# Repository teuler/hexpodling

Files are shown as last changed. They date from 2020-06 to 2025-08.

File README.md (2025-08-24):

# hexpodling
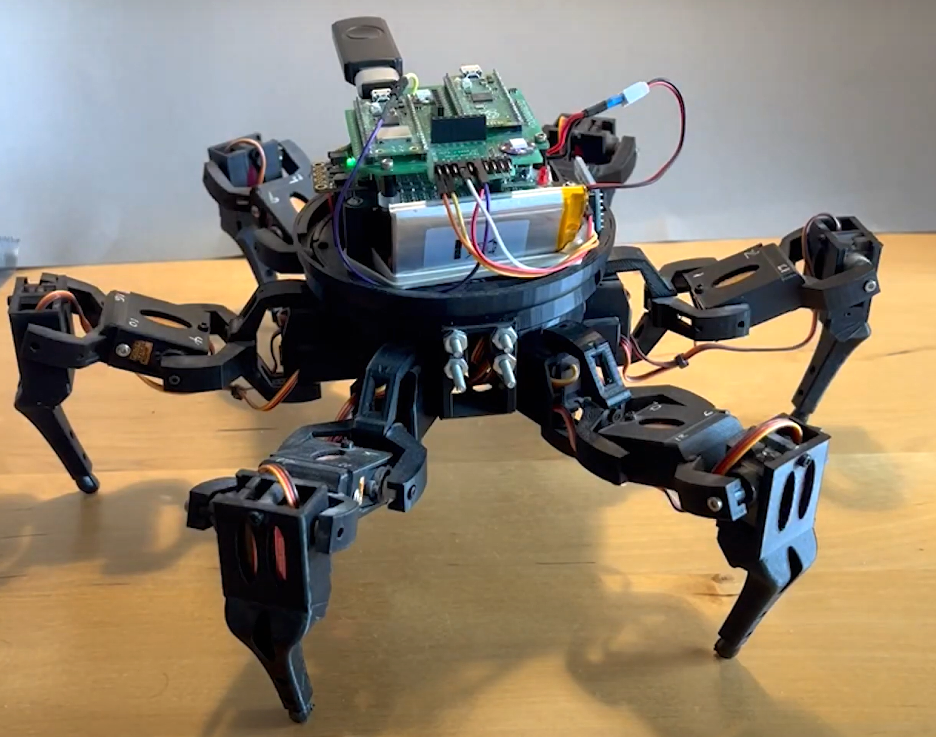
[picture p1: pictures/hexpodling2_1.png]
[](https://github.com/teuler/hexpodling/blob/master/pictures/hexpodling2_1.png)
"hexpodling" is a work-in-progress, 3-degrees of freedom (3DOF) hexapod robot based on the [Vorpal](https://vorpalrobotics.com/wiki/index.php/Vorpal_The_Hexapod) from Vorpal Robotics. The original Vorpal is remote-controlled and 2DOF; it is aimed at teaching in schools. 

The main differences between the original and the version described here are:
* The legs contain an additional segment, hence 3DOF
* Based on [Raspberry Pi Pico microcontrollers](https://www.raspberrypi.com/products/raspberry-pi-pico/) instead of the original's Arduino Nano, with one Pico controlling the movements (server) and one for the "higher" functions (client)
* Programmed in [PicoMite MMBasic](https://geoffg.net/picomite.html) by Peter Mather and Geoff Graham
* Supports current sensing (load) for up to 8 servos, e.g. to detect if the robot is stuck

Here is a [video](https://youtu.be/h_NlpfQ0yDU) demonstrating its movements (remote-controlled).  
For the details, see [Wiki](https://github.com/teuler/hexpodling/wiki).

### Release Notes

* 2025-08-24
  * Sensor head with camera (ESP32-cam) and time-of-flight distance sensor added (see [new wiki page](https://github.com/teuler/hexpodling/wiki/Camera-and-ToF-sensor))
  * new printed parts (sensor head) added
* 2025-01-01 - After a long pause
  * Switched to MMBasic :-)
  * New client board featuring two Pico RP2040 microcontrollers
  * Remote control (to test movements) direcly w/ a wireless XBox controller
* 2020-12-27 - Updates - Still work in progress
  * Wiki pages 'Mechanics' and 'Boards' added
  * Code updated (now also some initial code for the client microcontroller)
  * Both boards - for the "walk engine" and for the "behavior engine" - revised (including bug fixes)
* 2020-06-27 - Initial release

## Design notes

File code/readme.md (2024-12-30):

- `micropython` - the __depreciated__ python code
- `mmbasic`- the current MMBasic code w/ libraries and tools

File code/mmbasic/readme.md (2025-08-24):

This folder contains the current MMBasic code:

- `hps_calibrate.bas` - A tool to calibrate the servo positions of the legs
- `hps_cli.bas` - The main program for the Pico that serves as client (it controls the robot) 
- `hps_srv.bas` - The main program for the Pico that runs the server; it controls the movements of the robot (lets it walk), collects some sensor data about the robots orientation, the voltages of servo and logic batteries, etc.
- `lib_bno055.bas` - "Driver" for the BNO055 9-axis absolute-orientation sensor with sensor fusion.
- `lib_mcp3208.bas` - "Driver" for the MCP3208 chip, an 8-channel 12-bit A/D converter with SPI interface
- `lib_esp32cam.bas` - "Driver" for the ESP32-cam / VL53L5CX time-of-flight sensor
- `lib_keyboard.bas` - Keyboard routines for `hps_cli.bas`
- `lib_maestro.bas` - Routines for servo control via the Pololu 18-channel Maestro board
- `cal_load.dat` - calibration data for the first 4 servo load channels 

## Server
To upload the software to the server Pico:
1. Install the [PicoMite firmware](https://geoffg.net/Downloads/picomite/PicoMite_Firmware.zip) (V6.0x, `PicoMiteRP2350V6.0xxx.uf2`)
2. Load programs onto the internal drive:
   ```
   xmodem r "hps_srv.bas"
   xmodem r "lib_bno055.bas"
   xmodem r "lib_mcp3208.bas"
   xmodem r "lib_maestro.bas"
   xmodem r "hps_calibrate.bas"
   xmodem r "cal_load.dat"
   ```
3. Install libraries:
   ```
   library delete
   load "lib_bno055.bas"
   library save
   load "lib_mcp3208.bas"
   library save
   load "lib_maestro.bas"
   library save
   ```
4. Set the following options:
   ```
   OPTION COLOURCODE ON
   OPTION DISPLAY 64, 80   
   OPTION AUTORUN ON
   OPTION HEARTBEAT OFF
   OPTION CPUSPEED 252000
   ```
5. Now load the main program `hps_srv.bas` and run it.
     
## Client
To upload the software to the client Pico:
1. Install the [PicoMite firmware](https://geoffg.net/Downloads/picomite/PicoMite_Firmware.zip) (V6.0x, `PicoMiteRP2350USBV6.0xxx.uf2t). The USB variant is needed to allow the robot to be controlled by a USB-gamepad.

> Note: _After installing the USB firmware, the Pico console cannot be longer connected via the USB port, because it enters host-mode. For connecting the serial console, use pins GP8 and GP9 (COM2, 115200). For details, see MMBasic manual._

2. Load programs onto the internal drive:
   ```
   xmodem r "hps_cli.bas"
   xmodem r "lib_keyboard.bas"
   xmodem r "lib_esp32cam.bas"
   ```
3. Install libraries:
   ```
   library delete
   load "lib_keyboard.bas"
   library save
   ```
4. Set the following options (note that the SPI and LCDPANEL options are only needed if connecting a TFT display):
   ```
   OPTION SERIAL CONSOLE COM2,GP8,GP9
   OPTION LCD SPI GP18,GP19,GP16
   OPTION COLOURCODE ON
   OPTION HEARTBEAT OFF
   OPTION CPUSPEED 252000
   OPTION DISPLAY 64, 80
   OPTION LCDPANEL ST7789_320BUFF, PORTRAIT,GP22,GP15,GP17,GP14
   OPTION AUTORUN ON
   OPTION PICO OFF
   ```
   Calling `option list` should also give the follwing options automatically:
   ```
   OPTION SERIAL CONSOLE COM2,GP8,GP9
   OPTION KEYBOARD US
   ```
   
5. Now load the main program `hps_cli.bas` and run it.

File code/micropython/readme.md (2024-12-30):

The code in this folder is __depreciated__. It contains python code that runs on a PC, e.g. to communicate with a hexbotling:

- `hexapod_remote_ble.py` - Allows remote controlling the robot using a standard USB/wireless game controller. It translates the game controller actions into 
   walk/movement commands and sends them via a Bluetooth (BLE) link to the TinyPICO ESP32 on the robot. This program requires the Python packages 
   [`numpy`](https://numpy.org/), [`pygame`](https://www.pygame.org), and [`bleak`](https://github.com/hbldh/bleak).
   
The subfolder `hexbotling` contains the code that runs on the roboter.

The folder `modules` contains additional libraries (e.g. `joystick.py`)

> Note: _The robot code relies on the drivers in [`robotling_lib`](https://github.com/teuler/robotling_lib), which has to be clones into the `hexbotling` 
  folder on the development PC._

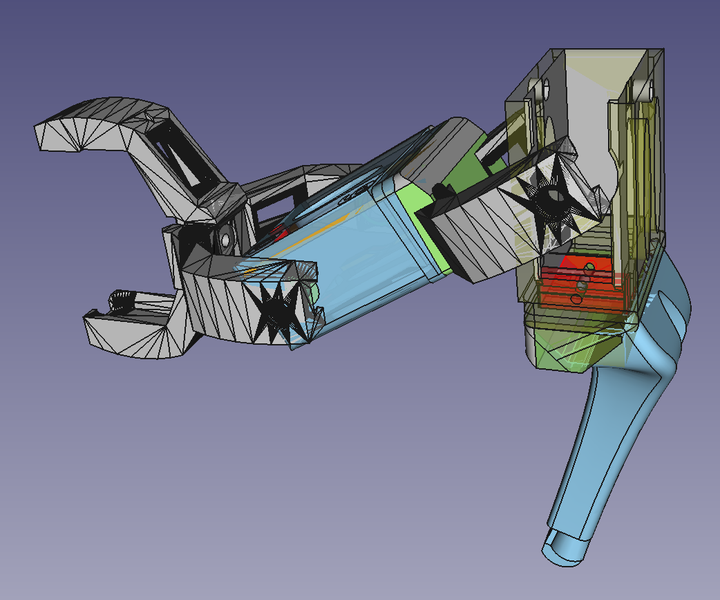
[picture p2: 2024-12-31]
pictures/3dof_leg_2a.png

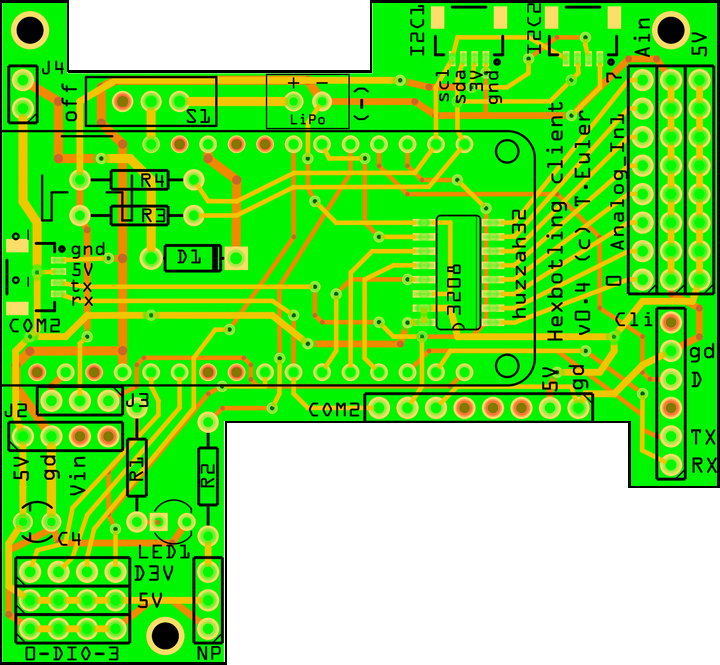
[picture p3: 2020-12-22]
pictures/hexpodling_client_v0_4.png

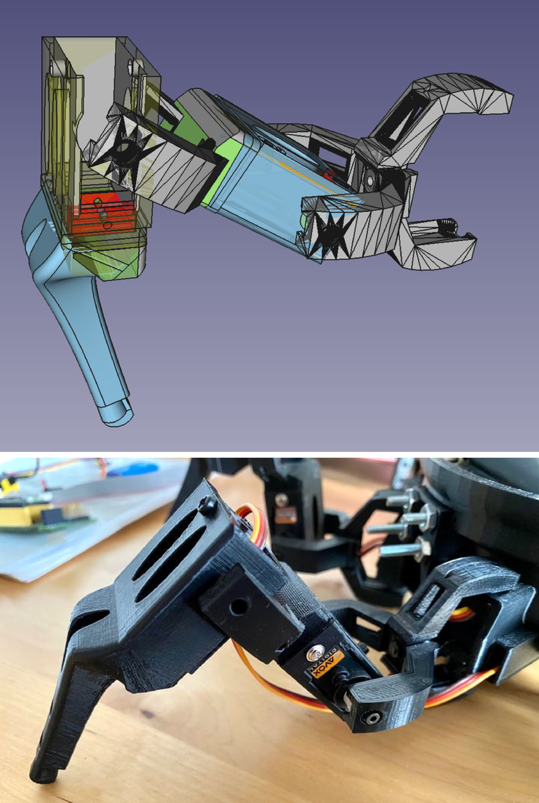
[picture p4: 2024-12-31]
pictures/leg.png

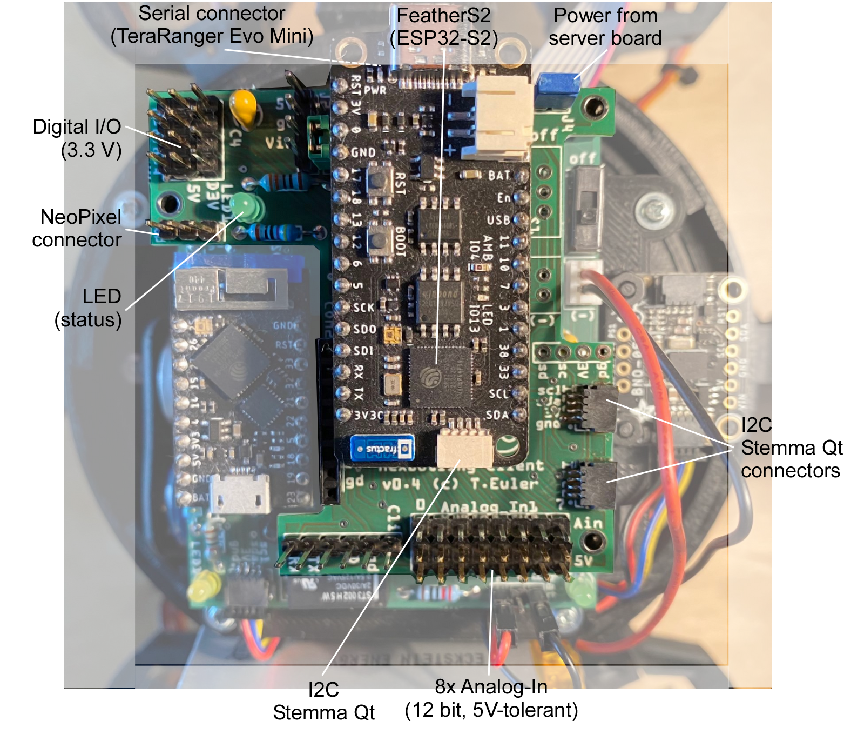
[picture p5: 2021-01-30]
pictures/Hexpodling_board2_v1.png

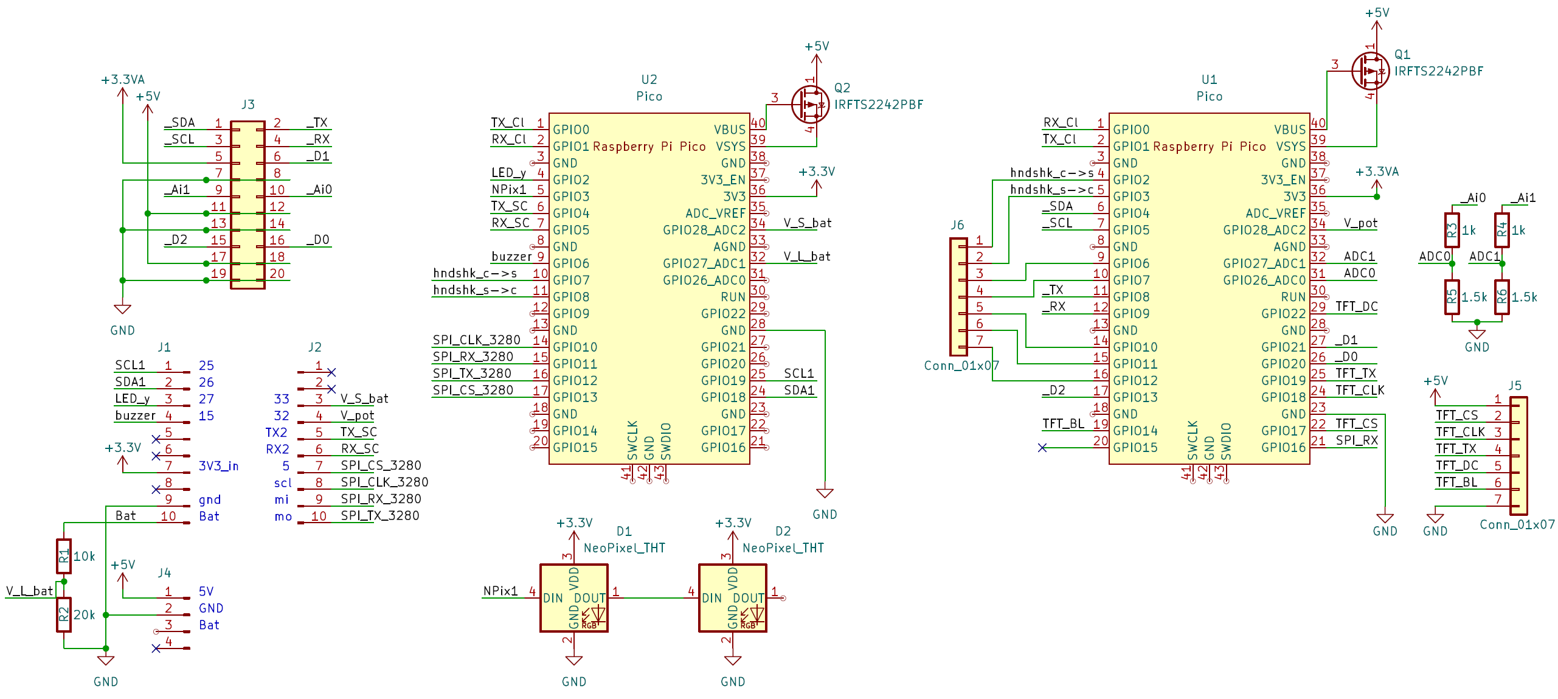
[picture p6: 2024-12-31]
pictures/circuit_hexbotling_client_v2.png

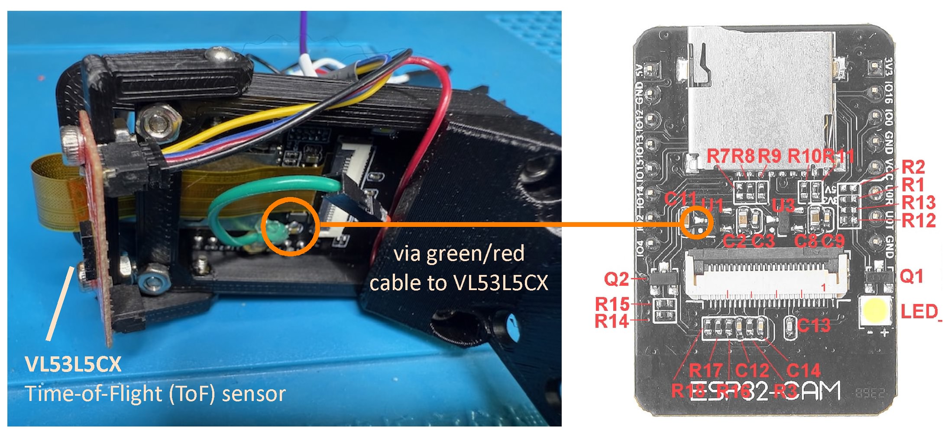
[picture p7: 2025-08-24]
pictures/Hexapod_board3_ESP32Cam_v1.jpg

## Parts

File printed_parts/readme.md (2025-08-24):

This folder contains the `.STL` files for the 3D printed parts. Most of the parts are derived from the parts of the [Vorpal](https://vorpalrobotics.com/wiki/index.php/Vorpal_Robotics) hexapod; for link to original `.STL` files, see [here](https://vorpalrobotics.com/wiki/index.php/Vorpal_The_Hexapod_Assembly_Instructions). For details on the modifications, see [Wiki](https://github.com/teuler/hexpodling/wiki/Mechanics).

### Body
* `base_v5.stl` - Body of the robot
* `lid_v1.stl` - "Lid" for body with space for battery and mounts for electronics caddy
* `electronic_caddy_v2.stl` - Caddy for electronics

### Legs
* `hinge_v1.stl`, `hinge_v1_alternative.stl` - Leg (coxa)
* `femur_v1.stl` - Leg (femur)
* `tibea_v1.stl`, `tibea_v1_alternative.stl` - Leg (tibea)
* `foot.stl` - Foot

### Sensor head
* `camera_holder_v2-lid.stl` - holds ESP32-cam board in place and fixes camera (lens)
* `camera_holder_v2-mount.stl` - mounts sensor head to front of robot
* `camera_holder_v2-tof_holder.stl` - holds ToF sensor board
* `camera_holder_v2-base.stl` - base of head, holds ESP32-cam board

### Other parts
* `switch_adapter.stl` - Adapter for power switch (original)
* `LED_holder.stl` - Fits a 3-mm LED into one of the holes of the base

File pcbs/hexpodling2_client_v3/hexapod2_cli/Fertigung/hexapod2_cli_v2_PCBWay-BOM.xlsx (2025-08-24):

 |  |  | xxxx xxxx xxxxx xxPCS BOM (Sample Bill of Materials)
Item # | *Designator | *Qty | Manufacturer | *Mfg Part # | Description / Value | *Package/Footprint | Type | Your Instructions / Notes
1 | C1,C2,C3 | 3 | Samsung Electro-Mechanics | CL31A106KAHNNNE | 25V 10uF X5R ±10% 1206 Multilayer Ceramic Capacitors MLCC - SMD/SMT ROHS | 1206 | SMD
2 | D1,D2 | 2 | OPSCO Optoelectronics | SK6805MICRO-J | SMD,2.4x2.7mm RGB LEDs(Built-in IC) ROHS | SMD,2.4x2.7mm | SMD
3 | D3,D4,D5 | 3 | Hubei KENTO Elec | KT-0805G | Emerald 0805 LED Indication - Discrete ROHS | 805 | SMD
4 | D6 | 1 | Hubei KENTO Elec | KT-0805R | 0805 LED Indication - Discrete ROHS | 805 | SMD
5 | J6 | 1 | G-Switch | GT-USB-7010AN | USB 2.0 5A 1 Horizontal attachment 16P Female -40℃~+85℃ Gold High conductivity copper Type-C SMD USB Connectors ROHS | SMD | SMD
6 | Q1 | 1 | VBsemi Elec | IRFTS9342TRPBF-VB | 30V 1 Piece P-Channel SOT23-6 MOSFETs ROHS | SOT23-6 | SMD
7 | R1 | 1 | UNI-ROYAL(Uniroyal Elec) | 0603WAJ0103T5E | 100mW Thick Film Resistors 75V ±100ppm/℃ ±5% 10kΩ 0603 Chip Resistor - Surface Mount ROHS | 0603 | SMD
8 | R2 | 1 | UNI-ROYAL(Uniroyal Elec) | 0603WAF2002T5E | 100mW Thick Film Resistors 75V ±100ppm/℃ ±1% 20kΩ 0603 Chip Resistor - Surface Mount ROHS | 0603 | SMD
9 | R3,R4,R7,R8,R9,R10 | 6 | UNI-ROYAL(Uniroyal Elec) | 0603WAF2002T5E | 250mW Thick Film Resistors 200V ±100ppm/℃ ±5% 1kΩ 1206 Chip Resistor - Surface Mount ROHS | 0603 | SMD
10 | R5,R6 | 2 | YAGEO | RC0603JR-071KL | 100mW Thick Film Resistors 75V ±100ppm/℃ ±5% 1kΩ 0603 Chip Resistor - Surface Mount ROHS | 0603 | SMD
11 | R11,R12 | 2 | UNI-ROYAL(Uniroyal Elec) | 0603WAF4701T5E | 100mW Thick Film Resistors 75V ±100ppm/℃ ±1% 4.7kΩ 0603 Chip Resistor - Surface Mount ROHS | 0603 | SMD
12 | R14,R17 | 2 | UNI-ROYAL(Uniroyal Elec) | 0603WAF4700T5E | 100mW Thick Film Resistors 75V ±100ppm/℃ ±1% 470Ω 0603 Chip Resistor - Surface Mount ROHS | 0603 | SMD
13 | R15,R16 | 2 | UNI-ROYAL(Uniroyal Elec) | 0603WAF5101T5E | 100mW Thick Film Resistors 75V ±100ppm/℃ ±1% 5.1kΩ 0603 Chip Resistor - Surface Mount ROHS | 0603 | SMD
14 | R18 | 1 | UNI-ROYAL(Uniroyal Elec) | 0805W8J0202T5E | 125mW Thick Film Resistors 150V ±100ppm/℃ ±5% 2kΩ 0805 Chip Resistor - Surface Mount ROHS | 0603 | SMD
15 | SW1,SW2 | 2 | XKB Connection | TS-1187A-B-A-B | None Without 50mA 5.1mm 100000 Times 160gf 12V 5.1mm 1.5mm Round Button Standing paste SPST SMD Tactile Switches ROHS | SMD,5.1x5.1 | SMD
16 | U2 | 1 | Microchip Tech | MCP73831T-2ACI/OT | 6V Lithium-ion/Polymer 1 500mA SOT-23-5 Battery Management ROHS | SOT-23-5 | SMD
Need a quick and accurante quote? Need an efficient production? Please read SMT Ordering Necessary Files & Info in 1 minute. Thank you very much! (https://www.pcbway.com/smt_ordering_guide.html)
Click for Instructions on How to Create a BOM (https://www.pcbway.com/blog/PCB_Assembly/How_to_Build_a_BOM__Bill_Of_Materials_.html)

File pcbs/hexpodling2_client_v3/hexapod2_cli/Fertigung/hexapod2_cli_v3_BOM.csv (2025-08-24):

Reference | Value | Footprint | Datasheet | Beschreibung | Qty | DNP
C1,C2,C3 | 10uF | Capacitor_SMD:C_1206_3216Metric_Pad1.33x1.80mm_HandSolder | ~ | Unpolarized capacitor, small symbol | 3
D1,D2 | SK6805 | LED_SMD:LED_SK6805_PLCC4_2.4x2.7mm_P1.3mm | https://cdn-shop.adafruit.com/product-files/3484/3484_Datasheet.pdf | SK6805 | 2
D3,D4,D5 | LED green | LED_SMD:LED_0805_2012Metric_Pad1.15x1.40mm_HandSolder |  | KT-0805G | 3
D6 | LED red | LED_SMD:LED_0805_2012Metric_Pad1.15x1.40mm_HandSolder |  | KT-0805R | 1
J6 | USB_C_Receptacle_USB2.0_16P | Connector_USB:USB_C_Receptacle_GCT_USB4105-xx-A_16P_TopMnt_Horizontal | https://www.usb.org/sites/default/files/documents/usb_type-c.zip | USB 2.0-only 16P Type-C Receptacle connector | 1
Q1 | IRFTS2242PBF | Package_SO:TSOP-6_1.65x3.05mm_P0.95mm | https://www.infineon.com/dgdl/irfts9342pbf.pdf?fileId=5546d462533600a40153563aeabc21f3 | IRFTS2242PBF | 1
R1 | 10k | Resistor_SMD:R_0603_1608Metric_Pad0.98x0.95mm_HandSolder | ~ |  | 1
R2 | 20k | Resistor_SMD:R_0603_1608Metric_Pad0.98x0.95mm_HandSolder | ~ |  | 1
R3,R4,R7,R8,R9,R10 | 1k | Resistor_SMD:R_0603_1608Metric_Pad0.98x0.95mm_HandSolder | ~ |  | 6
R5,R6 | 1.5k | Resistor_SMD:R_0603_1608Metric_Pad0.98x0.95mm_HandSolder | ~ |  | 2
R11,R12 | 4k7 | Resistor_SMD:R_0603_1608Metric_Pad0.98x0.95mm_HandSolder | ~ |  | 2
R14,R17 | 470 | Resistor_SMD:R_0603_1608Metric_Pad0.98x0.95mm_HandSolder | ~ |  | 2
R15,R16 | 5K1 | Resistor_SMD:R_0603_1608Metric_Pad0.98x0.95mm_HandSolder | ~ |  | 2
R18 | 2K | Resistor_SMD:R_0603_1608Metric_Pad0.98x0.95mm_HandSolder | ~ |  | 1
SW1 | BootSel | Button_Switch_SMD:SW_Push_1P1T_XKB_TS-1187A | ~ | TS-1187A | 1
SW2 | Reset | Button_Switch_SMD:SW_Push_1P1T_XKB_TS-1187A | ~ | TS-1187A | 1
U2 | MCP73831-2-OT | Package_TO_SOT_SMD:SOT-23-5 | http://ww1.microchip.com/downloads/en/DeviceDoc/20001984g.pdf | Single cell, Li-Ion/Li-Po charge management controller, 4.20V, Tri-State Status Output, in SOT23-5 package | 1

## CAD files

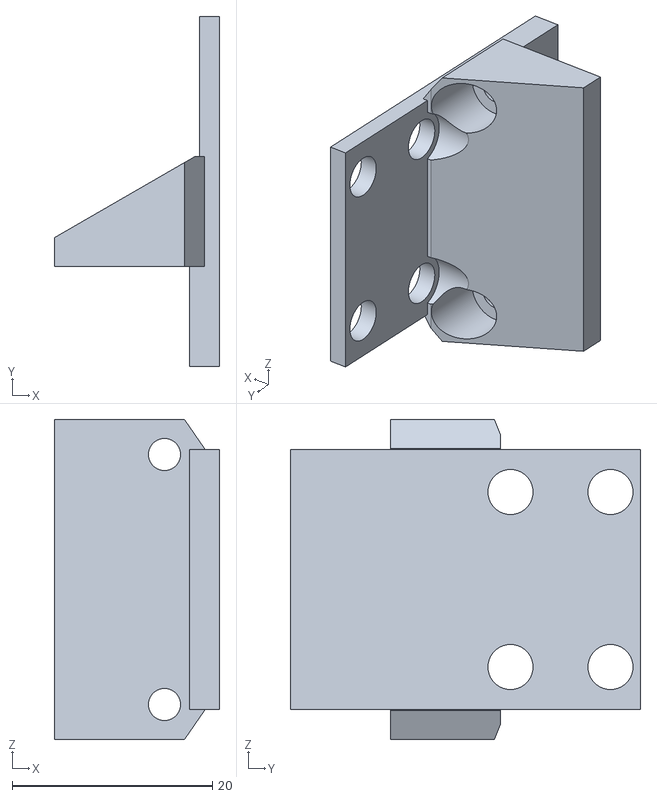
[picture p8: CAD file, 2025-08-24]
printed_parts/camera_holder_v2-mount.stl
16.5 x 35.0 x 32.0

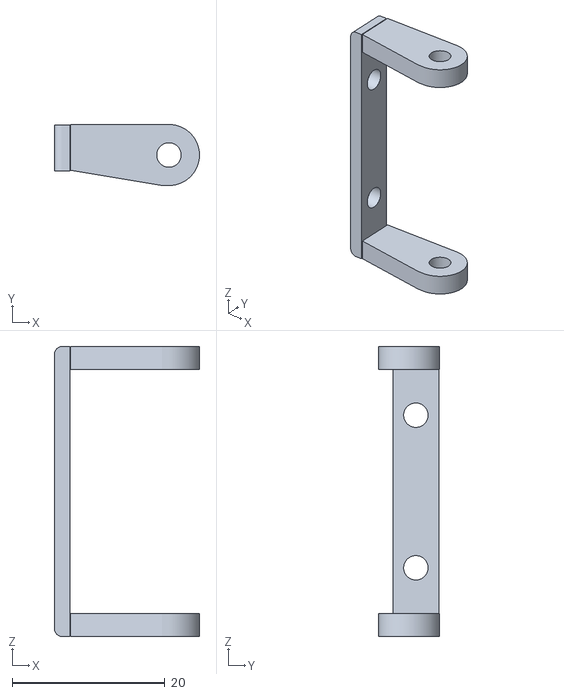
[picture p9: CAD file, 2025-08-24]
printed_parts/camera_holder_v2-tof_holder.stl
19.0 x 8.00 x 38.0

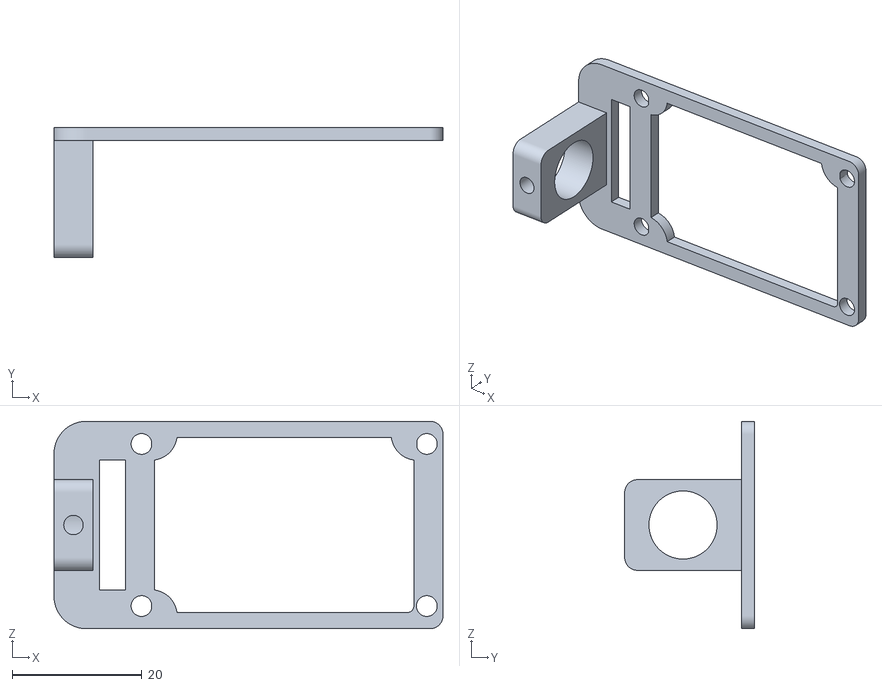
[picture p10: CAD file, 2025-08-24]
printed_parts/camera_holder_v2-lid.stl
60.0 x 20.0 x 32.0

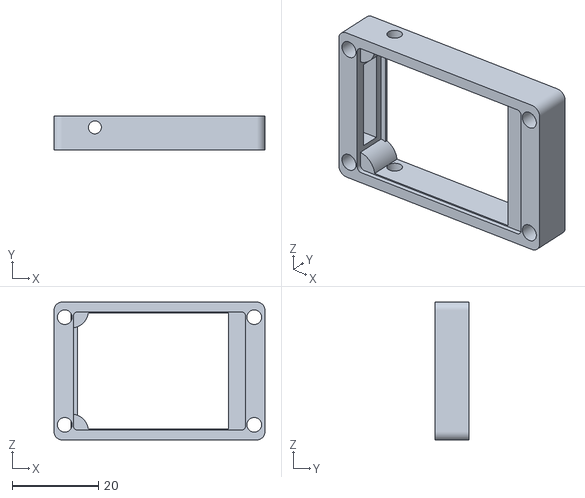
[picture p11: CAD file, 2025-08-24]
printed_parts/camera_holder_v2-base.stl
49.0 x 8.00 x 32.0

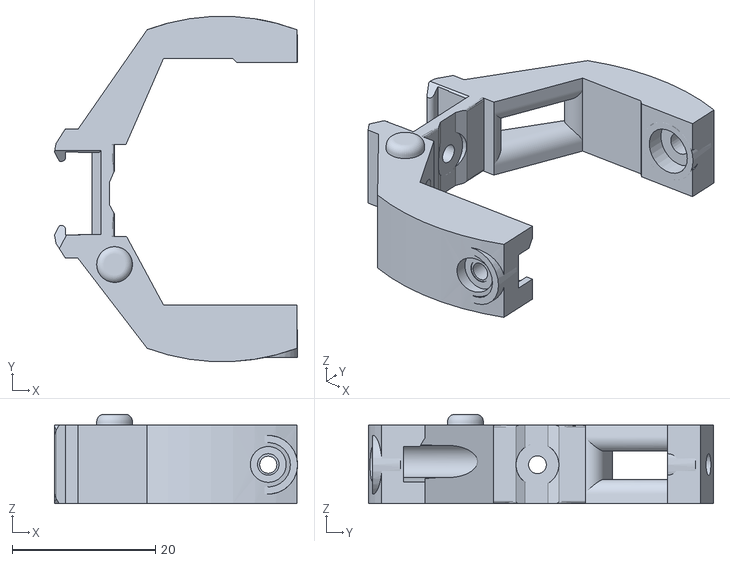
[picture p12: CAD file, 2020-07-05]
printed_parts/hinge_v1_alternative.stl
34.0 x 48.2 x 12.5

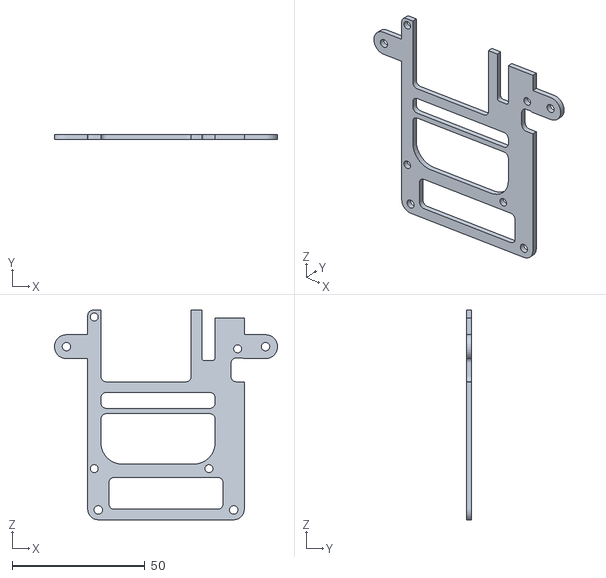
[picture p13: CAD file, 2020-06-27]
printed_parts/electronics_caddy_v2.stl
84.0 x 2.00 x 79.0

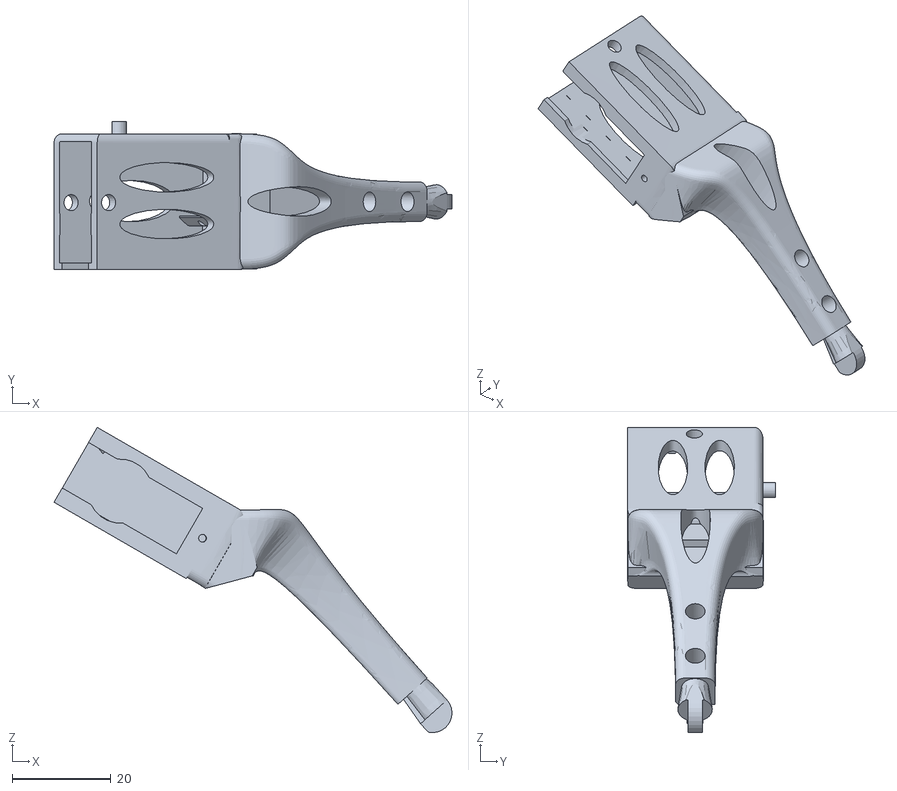
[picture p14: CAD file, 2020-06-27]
printed_parts/tibea_v1.stl
80.7 x 30.0 x 61.9

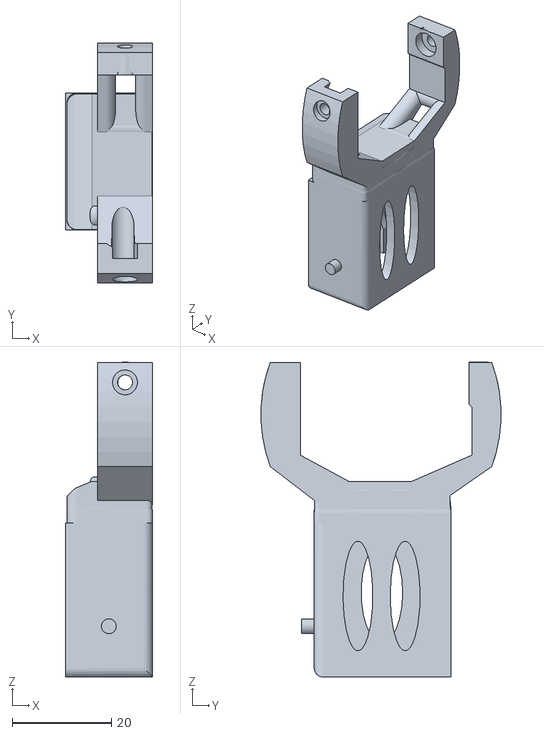
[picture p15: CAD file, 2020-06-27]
printed_parts/femur_v1.stl
17.6 x 48.2 x 63.4

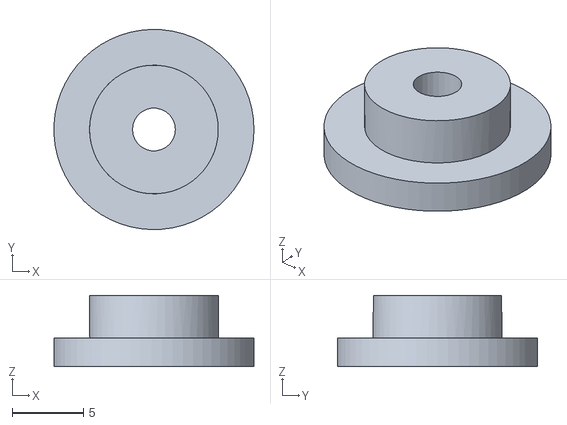
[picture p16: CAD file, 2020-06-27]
printed_parts/LED_holder.stl
14.0 x 14.0 x 5.00

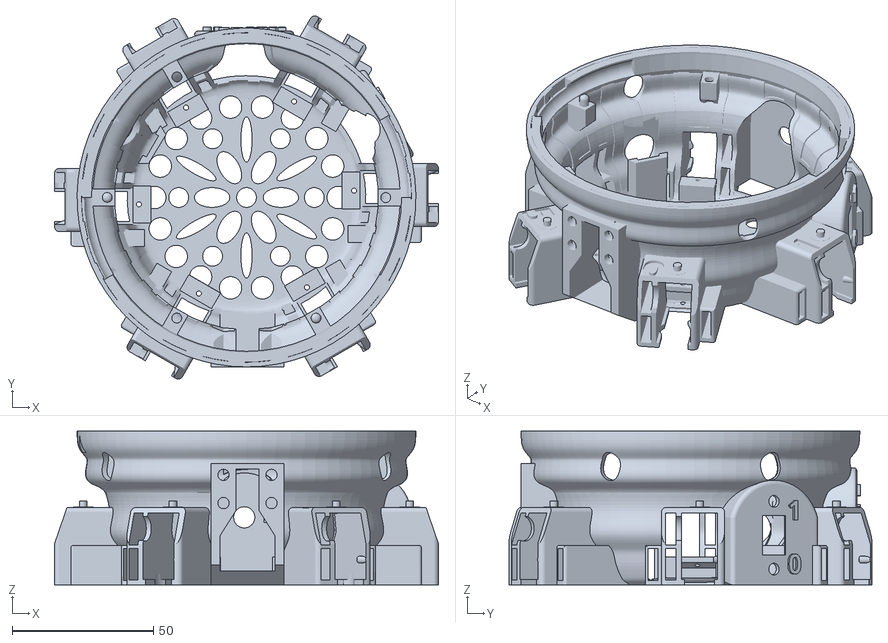
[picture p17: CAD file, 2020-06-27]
printed_parts/base_v5.stl
136.0 x 128.6 x 54.4

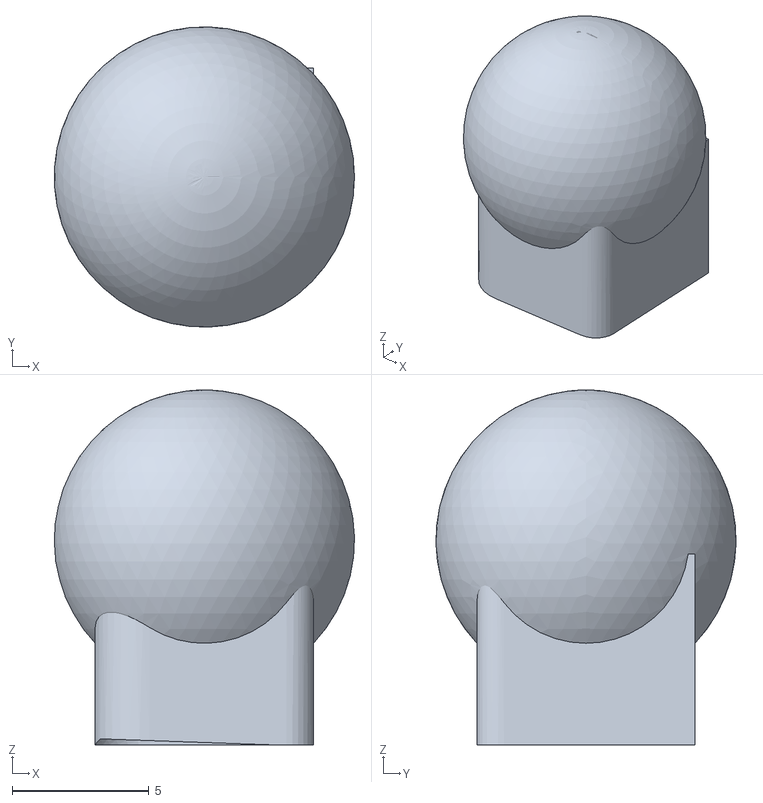
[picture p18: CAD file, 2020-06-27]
printed_parts/foot.stl
11.0 x 11.0 x 13.0

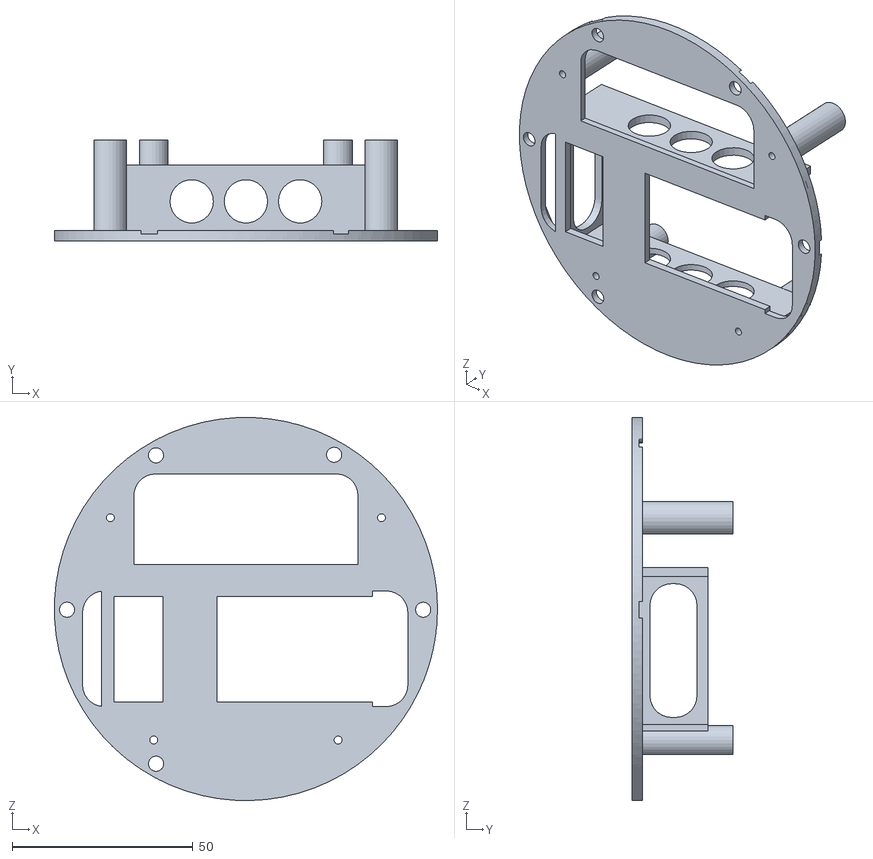
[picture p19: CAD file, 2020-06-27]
printed_parts/lid_v1.stl
106.0 x 28.0 x 106.0

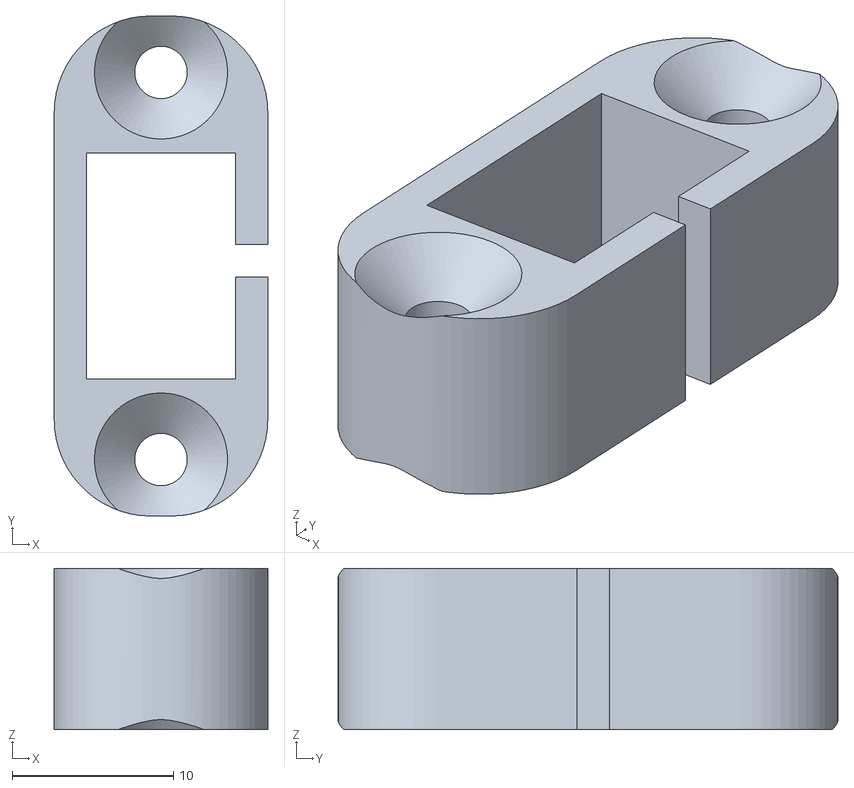
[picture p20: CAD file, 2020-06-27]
printed_parts/switch_adapter.stl
13.2 x 31.0 x 10.0

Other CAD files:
printed_parts/hinge_v1.stl
printed_parts/tibea_v1_alternative.stl

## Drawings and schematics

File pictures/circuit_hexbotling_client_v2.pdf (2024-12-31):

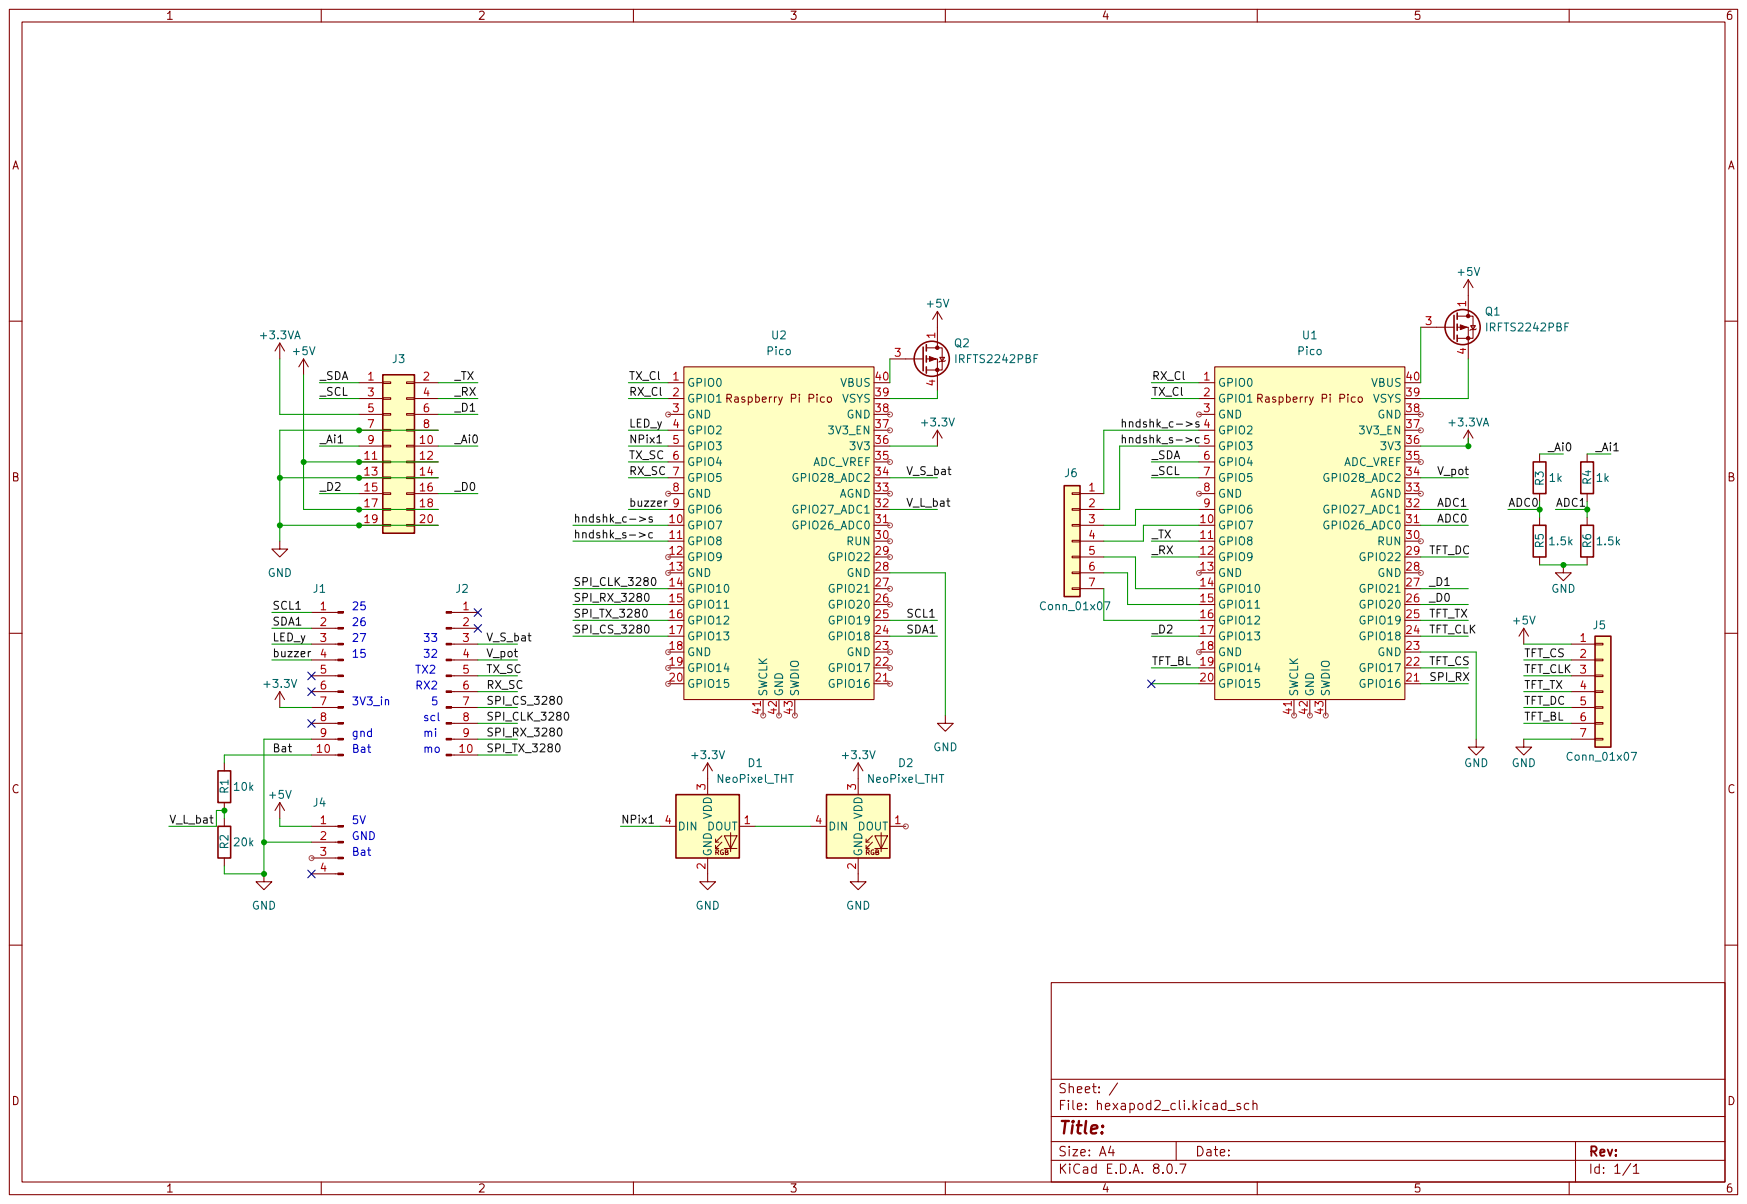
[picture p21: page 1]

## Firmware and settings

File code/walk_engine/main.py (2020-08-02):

# ----------------------------------------------------------------------------
# main.py
# Main program; is automatically executed after reboot.
#
# The MIT License (MIT)
# Copyright (c) 2020 Thomas Euler
# 2020-01-06, First version
#
# ----------------------------------------------------------------------------
from time import ticks_ms
from hexapod import *

# ----------------------------------------------------------------------------
def main():
  # Setup the walk engine's spin function
  r.spin_ms(period_ms=r.Cfg.TM_PERIOD, callback=r.housekeeper)
  r.spin_ms(100)

  # Loop ...
  print("Entering loop ...")
  try:
    try:
      round = 0
      isDone = False

      while True:
        try:
          # Check if dial has changed
          if r._dialChanged:
            r._dialChanged = False
            if r._currDialPos in [0,3]:
              if r._currDialPos == 0:
                # Stop GGN, assume sitting position and power-down
                r.GGN.stop()
                r.setPosture(post=r.POST_SITTING)
                r.servoPower = False
                r._hexState = HexState.Stop
              elif r._currDialPos == 1:
                pass
                '''
                # Power up and assume a neutral position
                r.servoPower = True
                r.setPosture(post=r.POST_NEUTRAL)
                r._hexState = HexState.Adjust
                '''
              elif r._currDialPos == 3:
                # Activate GGN
                r.servoPower = True
                r.setPosture(post=r.POST_WALK)
                r.GGN.start()
                r._hexState = HexState.WalkEngineEngaged
              toLog("Dial=={0} -> {1}"
                    .format(r._currDialPos, HexStateStr[r._hexState]))

          # Check for new command
          if r._hexState == HexState.WalkEngineEngaged and r.mIn.receive():
            # Handle command ...
            isDone = r.onSerialCommand()
            if not isDone:
              toLog("Command not handled", ErrCode.Cmd_NotHandled)
          elif not r.mIn.error == rmsg.Err.Ok:
            toLog("Error parsing command", ErrCode.Cmd_ParsingErr)
            r.Buzzer.warn()

        finally:
          # Keep GGN running and make sure the robot's housekeeping gets
          # updated once per loop
          if r._hexState == HexState.WalkEngineEngaged:
            r.GGN.spin()
          r.spin_ms()
          round += 1

    except KeyboardInterrupt:
      r.isRunning = False
      print("Loop stopped.")

  finally:
    # Power down ...
    r.powerDown()
    r.printReport()

# ----------------------------------------------------------------------------
# Create instance of HexaPod, derived from the WalkEngine class
r = HexaPod()

# Call main
if __name__ == "__main__":
  try:
    main()
  except Exception as e:
    # Create an in-memory file-like string object (`sIO`) to accept the
    # exception's traceback (`sys.print_exception` requires a file-like
    # object). This traceback string is then converted into a dictionary
    # to be sent as an MQTT message (if telemetry is activate)
    if r.Tele and r.Tele.connected:
      import sys, uio
      sIO = uio.StringIO()
      sys.print_exception(e, sIO)
      r.Tele.publishDict(KEY_RAW, {KEY_DEBUG: str(sIO.getvalue())})
    # Re-raise the exception such that it becomes also visible in the REPL
    raise e

# ----------------------------------------------------------------------------

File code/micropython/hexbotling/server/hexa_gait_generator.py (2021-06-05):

#!/usr/bin/env python
# -*- coding: utf-8 -*-
# ----------------------------------------------------------------------------
# hexa_gait_generator.py
# Gait generator (GGN) class
#
# The MIT License (MIT)
# Copyright (c) 2020-21 Thomas Euler
# 2020-04-02, First version
# 2021-01-18, Foot positions captured
# ----------------------------------------------------------------------------
import array
import math
try:
  ModuleNotFoundError
except NameError:
  ModuleNotFoundError = ImportError
try:
  # Micropython imports
  from micropython import const
  from time import ticks_ms, ticks_diff
  from hexa_global import *
  from server.hexa_gait import HexaGait
  from server.hexa_input import HexaInput
  from robotling_lib.misc.helpers import timed_function
  from ulab import numpy as np
except ModuleNotFoundError:
  # Standard Python imports
  const = lambda x : x
  from time import time_ns as ticks_ms
  from hexbotling.hexa_global import *
  from hexbotling.server.hexa_gait import HexaGait
  from hexbotling.server.hexa_input import HexaInput
  import numpy as np

# ----------------------------------------------------------------------------
class HexaGaitGenerator(object):
  """ Gait generator (GGN) control and status parameters
  """
  def __init__(self, config, led, servo_man, verbose=0):
    # Initialize
    self._isReady = False
    self._verboseLevel = verbose
    self._Cfg = config
    assert servo_man is not None, "Why is no servo manager defined?"
    self._SMan = servo_man
    self._LED = led
    self._Gait = HexaGait()
    self._Inp = HexaInput(self._Gait, config)
    self.reset()
    self._isReady = True
    toLog("Gait generator (GGN) initialized.")

  # - - - - - - - - - - - - - - - - - - - - - - - - - - - - - - - - - - - - -
  def reset(self):
    """ Reset gait generator
    """
    # Initialize GGN control parameters
    self.isOnPrev         = False          # Previous state of GGN on/off switch
    self.state            = GGNState.Idle  # Current and next state of GGN
    self.nextState        = self.state
    self.moveDur_ms       = 0              # Duration of current, next and
    self.lastMoveDur_ms   = 0              # previous move
    self.nextMoveDur_ms   = 0
    self.calcDur_ms       = 0              # Duration of last GGN calculation
    self.waitUntil_ms     = 0

    # Quality control-related
    self.tMoveStart_ms    = 0              # Time when move last was started
    self.lastMoveLate_ms  = 0              # Delay of the last executed move
    self.lastIKSolRes     = GGN_IKM_None   # Last IK solution results
                                           # =errors*100 +warnings*10 +solutions
    # Reset input parameters
    self._Inp.reset(self._Gait)

    # Set start position of each foot
    self._xyzLegPos = np.array(self._Cfg.FEET_INIT_XYZ)
    self._allLegsDown = True

    # Current leg angles from IK and converted into servo angles
    self._legAngles = np.zeros((LEG_COUNT, 3))
    self._servoAngles = np.zeros((LEG_COUNT, 3))

    # Current foot positions
    self._xyzCurrFootPos = np.zeros((LEG_COUNT, 3), dtype=np.int16)

    # General state and error
    self.walkEngineState = WEState.Standby
    self.lastErrC = ErrCode.Ok
    self._prevStates = [self.state, self.walkEngineState, self.lastErrC]

  def change_gait(self, gaitType=GGN_GAIT_default):
    """ Set or change the gait type
    """
    # TODO: Make sure that robot has stopped
    if gaitType != self._Gait._type:
      self._Gait = HexaGait(gaitType)
      self.reset()

  # - - - - - - - - - - - - - - - - - - - - - - - - - - - - - - - - - - - - -
  def start(self):
    """ Start GGN
    """
    self._Inp.prepare(True)
    self.state = GGNState.NeedsToCompute
    self.walkEngineState = WEState.Ready
    self.log_status()

  def stop(self):
    """ Stop GGN
    """
    self._Inp.prepare(False)
    self.state = GGNState.Idle
    self.walkEngineState = WEState.Standby
    self.log_status()

  def spin(self):
    """ Call frequently to keep GGN running
    """
    if self.state == GGNState.IsMoving:
      # Still executing the last move
      if self.waitUntil_ms > 0 and ticks_ms() > self.waitUntil_ms:
        # Change state to trigger execution of the next move
        self.state = GGNState.UpdateServos
        self.waitUntil_ms = 0

    if self.state == GGNState.NeedsToCompute:
      # Calculate next move and set timer for move execution
      # -> `IsMoving` or, if delay is too short, `NeedsToCompute`
      self._LED.on()
      self._compute_next_move()
      self._LED.off()

    elif self.state == GGNState.UpdateServos:
      # Previous move is finished, now commit next move
      # -> `NeedsToCompute`
      self._execMove()

    elif self.state == GGNState.Idle:
      # `IsMoving`, Timer -> `UpdateServos`
      pass
    if self._verboseLevel > 0:
      self.log_status()

  # - - - - - - - - - - - - - - - - - - - - - - - - - - - - - - - - - - - - -
  #@timed_function
  def _compute_next_move(self):
    """ Compute the next move
    """
    # Initialize
    t1_ms = ticks_ms()
    cfg = self._Cfg
    inp = self._Inp
    gait = self._Gait
    self.lastIKSolRes = GGN_IKM_None
    self.lastErrC = ErrCode.Ok

    # Do some checking ...
    if inp.doEmergStop:
      # TODO
      raise NotImplementedError("Not yet implemented")
    if inp.controlMode is not GGN_MODE_walk:
      # TODO
      raise NotImplementedError("only `GGN_MODE_walk` implemented")

    # Update input parameters with blending
    inp.update_blending()
    y = max(inp.bodyYOffs.val +inp.bodyYShift.val, 0)
    v = inp.xyzBodyPos.val
    inp.xyzBodyPos.val = [v[0], y, v[2]]

    # Check if target angle is set and compass is on, if so, handle it
    if inp.tarAngle_deg != GGN_InvalidAngle and False:
      # TODO
      raise NotImplementedError("`tarAngle_deg` not yet implemented")
      '''
      if(abs(inputGGN.tarAngle_deg -EXB.compassDir) < cTurnDeadZone_deg) {
        // target angle and compass angle are virtually the same, thus reset
        // target angle and stop turning
        inputGGN.tarAngle_deg = GGN_InvalidAngle;
        inputGGN.travelRotY = 0;
        currFlags = (currFlags & ~HXA_flag_isTurnToTarget); }
      else {
        // Set flag to indicate that the target direction is not yet reached
        currFlags = (currFlags | HXA_flag_isTurnToTarget);
      }
      '''
    # Check if all legs are down and if not so, set them to their initial position
    self._allLegsDown = self._are_legs_down()
    if not self._allLegsDown:
      self._xyzLegPos = np.array(self._Cfg.FEET_INIT_XYZ)

    # Calculate update of gate sequence
    gait.isGaitInMotion = self._is_gait_in_motion()
    for iLeg in range(LEG_COUNT):
      gait._generate_leg_gait_seq(self, iLeg)
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

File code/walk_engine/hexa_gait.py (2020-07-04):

#!/usr/bin/env python
# -*- coding: utf-8 -*-
# ----------------------------------------------------------------------------
# hexa_gait.py
# Gait class
#
# The MIT License (MIT)
# Copyright (c) 2020 Thomas Euler
# 2020-04-02, First version
#
# ----------------------------------------------------------------------------
import math
try:
  ModuleNotFoundError
except NameError:
  ModuleNotFoundError = ImportError
try:
  # Micropython imports
  from micropython import const
  from hexa_global import *
  from misc.helpers import timed_function
  import ulab as np
except ModuleNotFoundError:
  # Standard Python imports
  const = lambda x : x
  import numpy as np
  from walk_engine.hexa_global import *

# ----------------------------------------------------------------------------
class HexaGait(object):
  """ Gait description and status parameters
  """
  def __init__(self, type=GGN_GAIT_default):
    # Initialize
    self._type = type
    self.reset()

  def reset(self):
    self.iGaitStep           = 1     # Index of current gait step
    self.iGaitLegIn          = 0     # Input number of the leg
    self.isGaitInMotion      = False # Gait is in motion
    self.isLastLeg           = False # Current leg is last leg of the sequence

    # Relative X,Y,Z positions, y rotations and initial leg positions
    self.xyzPos = np.zeros((LEG_COUNT, 3))
    self.rotY = np.zeros(LEG_COUNT)
    self.legNr = np.zeros(LEG_COUNT)

    if self._type == GGN_GAIT_default:
      # Tripod 6-steps (= gait type 4 in Phoenix code)
      self.nStepsInGait      = 8     # Number of steps in gait
      self.legLiftHeightDef  = 50    # Default travel height
      self.isHalfLiftHeigth  = True  # Outer positions of lifted half height
      self.TLDivFact         = 4     # n steps w/ leg on the floor (walking)
      self.nPosLifted        = 3     # n positions single leg is lifted (1-3)
      self.nomSpeed          = 70    # Nominal speed of the gait
      self.legNr[LEG_LR]     = 5     # Initial leg positions ...
      self.legNr[LEG_RF]     = 1
      self.legNr[LEG_LM]     = 1
      self.legNr[LEG_RR]     = 1
      self.legNr[LEG_LF]     = 5
      self.legNr[LEG_RM]     = 5

  # - - - - - - - - - - - - - - - - - - - - - - - - - - - - - - - - - - - - -
  #@timed_function
  def _generate_leg_gait_seq(self, GGN, iLeg):
    """ Generate the gait sequence for the selected leg
    """
    # Initialize
    inp = GGN._Inp
    isGIM = self.isGaitInMotion
    iStep = self.iGaitStep
    nStep = self.nStepsInGait
    nPosL = self.nPosLifted
    xyzGP = self.xyzPos[iLeg]
    yGR = self.rotY[iLeg]
    legNr = self.legNr[iLeg]
    tdl = self.TLDivFact

    # If gait is not in motion, reset travel parameters
    if not isGIM:
      inp.x_zTravelLen.val = [0,0,0]
      inp.travelRotY.val = 0

    # Leg middle up position
    if ((isGIM and (nPosL == 1 or nPosL == 3) and iStep == legNr) or
        (not isGIM and (iStep == legNr) and
         ((abs(xyzGP[0]) > 2) or (abs(xyzGP[2]) > 2) or (abs(yGR) > 2)))):
      # Up ...
      y = -inp.legLiftHeight.val
      self.xyzPos[iLeg] = np.array([0, -inp.legLiftHeight.val, 0])
      self.rotY[iLeg] = 0

    else:
      # Optional half heigth rear
      if (isGIM and
          ((nPosL == 2 and iStep == legNr) or
           (nPosL == 3 and
            (iStep == legNr -1 or
             iStep == legNr +nStep -1)))):
        lh = inp.legLiftHeight.val
        self.xyzPos[iLeg,0] = -inp.x_zTravelLen.x /2
        self.xyzPos[iLeg,1] = -lh/2 if self.isHalfLiftHeigth else -lh
        self.xyzPos[iLeg,2] = -inp.x_zTravelLen.z /2
        self.rotY[iLeg] = -inp.travelRotY.val /2

      else:
        # Optional half heigth front
        if (isGIM and nPosL >= 2 and
            (iStep == legNr +1 or
             iStep == legNr -(nStep -1))):
          lh = inp.legLiftHeight.val
          self.xyzPos[iLeg,0] = inp.x_zTravelLen.x /2
          self.xyzPos[iLeg,1] = -lh/2 if self.isHalfLiftHeigth else -lh
          self.xyzPos[iLeg,2] = inp.x_zTravelLen.z /2
          self.rotY[iLeg] = inp.travelRotY.val /2
        else:
          # Leg front down position
          if((iStep == (legNr +nPosL) or
              iStep == (legNr -(nStep-nPosL))) and xyzGP[1] < 0):
            self.xyzPos[iLeg,0] = inp.x_zTravelLen.x /2
            self.xyzPos[iLeg,1] = 0
            self.xyzPos[iLeg,2] = inp.x_zTravelLen.z /2
            self.rotY[iLeg] = inp.travelRotY.val /2
          else:
            # Move body forward
            self.xyzPos[iLeg,0] = xyzGP[0] -inp.x_zTravelLen.x /tdl
            self.xyzPos[iLeg,1] = 0
            self.xyzPos[iLeg,2] = xyzGP[2] -inp.x_zTravelLen.z /tdl
            self.rotY[iLeg] -= inp.travelRotY.val /tdl

    # Advance to the next step
    if iLeg == (LEG_COUNT -1):
      self.iGaitStep += 1
      if self.iGaitStep > nStep:
        self.iGaitStep = 1

  # - - - - - - - - - - - - - - - - - - - - - - - - - - - - - - - - - - - - -
  def _is_step_complete(self):
    """ Checks if GGN has not finished the last move
    """
    raise NotImplementedError("_is_step_complete")
    '''
    int gaitPeak = 0;
    // Finding any incident of GaitPos/Rot <>0
    //
    for(byte iL=0; iL<nLegs; iL+=1) {
      if(gaitPeak < abs(currGait.gaitPos[iL].x))
        gaitPeak = abs(currGait.gaitPos[iL].x);
      else
      if(gaitPeak < abs(currGait.gaitPos[iL].y))
        gaitPeak = abs(currGait.gaitPos[iL].y);
      else
      if(gaitPeak < abs(currGait.gaitPos[iL].z))
        gaitPeak = abs(currGait.gaitPos[iL].z);
      else
      if(gaitPeak < abs(currGait.gaitRotY[iL]))
        gaitPeak = abs(currGait.gaitRotY[iL]);
    }
    return (gaitPeak > 2);
    '''

# ----------------------------------------------------------------------------

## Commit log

2020-06-27 Picture of board
2020-06-27 Printed parts
    [LED_holder.stl, base_v5.stl, electronic_caddy_v1b.stl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]
2020-06-27 New caddy
    [electronic_caddy_v1b.stl, electronics_caddy_v2.stl]
2020-07-04 New pictures
    [hinge_v1.stl]
2020-12-22 PCB boards added
    [hexbotling_client_v0_4.fzz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]
2020-12-28 Board update (server)
    [hexbotling_v0_4.fzz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]
2020-12-29 Board update
    [hexbotling_v0_4.fzz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]
2021-01-30 Update boards
    [hexbotling_v0_4.fzz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]
2025-08-24 PCBs for client board v3 added
    [hexapod2_cli-B_Cu.gbr, hexapod2_cli-B_Mask.gbr, hexapod2_cli-B_Paste.gbr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]
2025-08-24 PCB for client v3
    [hexapod2_cli-B_Cu.gbr, hexapod2_cli-B_Mask.gbr, hexapod2_cli-B_Paste.gbr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]
2025-08-24 New printed parts
    [camera_holder_v2-base.stl, camera_holder_v2-lid.stl, camera_holder_v2-mount.stl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]
